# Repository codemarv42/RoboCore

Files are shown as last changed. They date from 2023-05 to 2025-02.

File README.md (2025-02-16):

# RoboCore

The RoboCore is basically a dual PCB solution, which is mounted on a chassis and takes over the evaluation and control of sensors and motors. Furthermore, this project was created by several people to develop the best robot for the RoboCup in the Rescue Line division. 

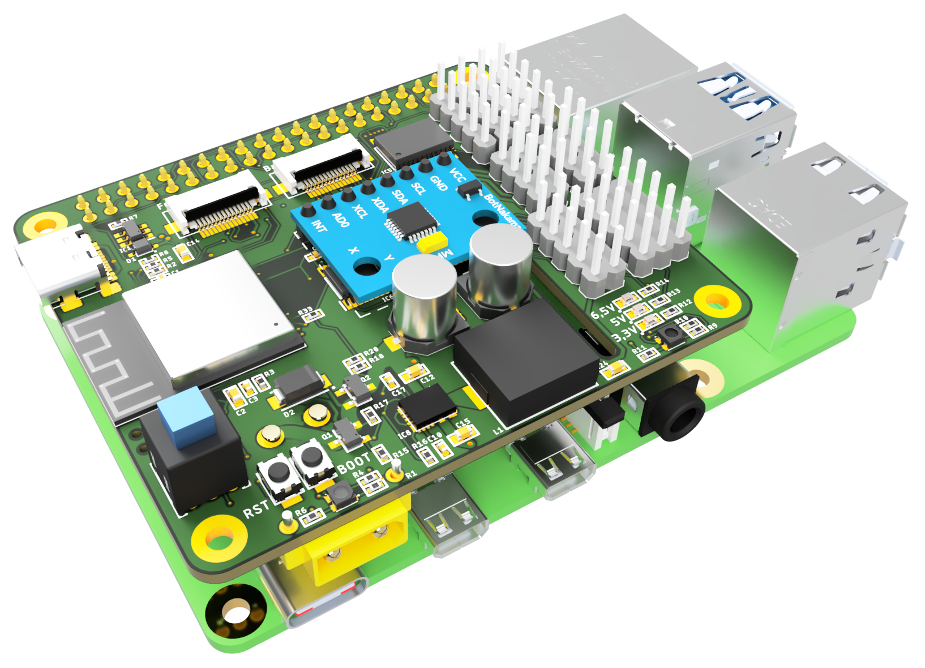
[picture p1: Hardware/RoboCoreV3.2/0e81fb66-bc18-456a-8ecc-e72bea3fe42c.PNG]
RoboCore V3.2


RoboCore embedded

# Hardware

A combination of two PCBs is used as our hardware, where the main PCB (RoboCoreV3.2) is plugged onto a Raspberry Pi and therefore forms the main control unit. The second circuit board (RoboLightV4.2) is installed on the underside of the robot and is responsible for measuring the light values on the line track. Below is our current hardware combination.

## To do list

- [x] Find Upload issue
- [x] Implement Boot and EN Buttons
- [x] Find ADC issue when using Neopixel LEDs
- [x] Voltage state LEDs
- [x] Inconsistent red-green difference of the LEDs

## Changelog

RoboCore:

- V3.2: Remove Neopixel led because of ADC problems, better voltage regulator for motor driver and further power management features
- V3.1: Raspberry PI hat design, external Display and buttons as user interface, ESP32-S3, two motor driver, Neopixel LED, Voltage regulator update
- V2: MPU6050 as secound PCB, dual light sensor bar, Pullup Fix near buttons
- V1: Inital Version

RoboLight:

- V4.3: Swap FCP pinout
- V4.2: Use regular RGB LEDs instead, better LED and phototransistor arrangement
- V4.1: Use Neopixel RGB LEDs instead, remove center photo transistor
- V3: Control Leds individual via a shiftregister
- V2: Fix distance between inner photo transistors
- V1: Inital Version

## Control unit PCB

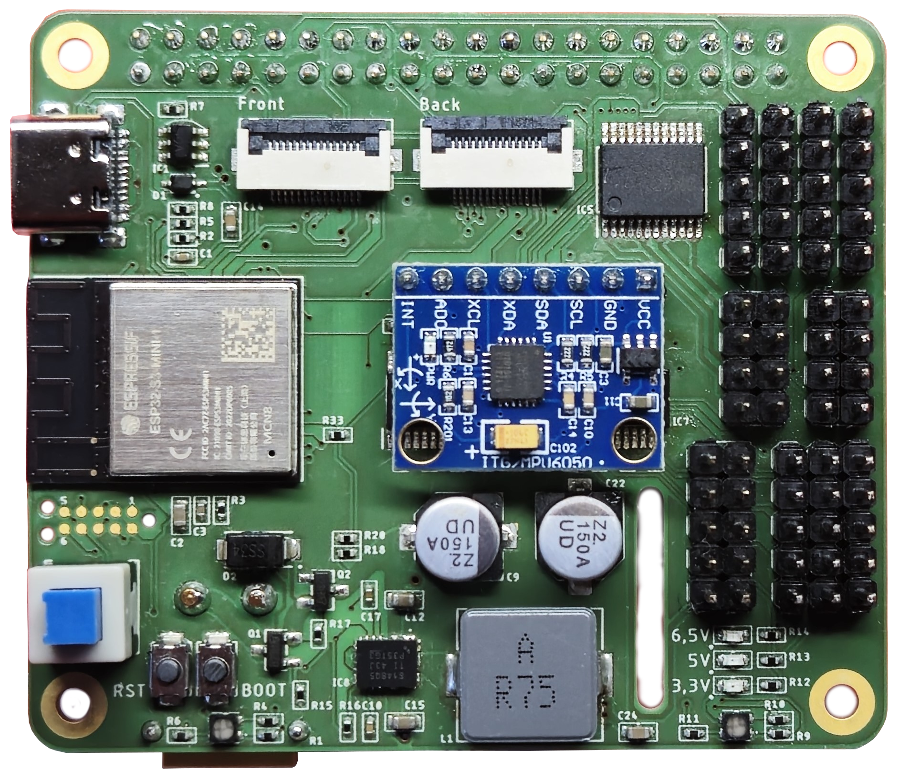
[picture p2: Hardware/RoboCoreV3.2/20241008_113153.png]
RoboCoreV3.2


Parameter for PCB (RoboCoreV3.2):

- Layer: 4
- Thickness: 1,6mm
- Length: 65,05mm
- Height: 56,03mm
- Minimum Copper Trace Width: 0,125mm

Pinout:

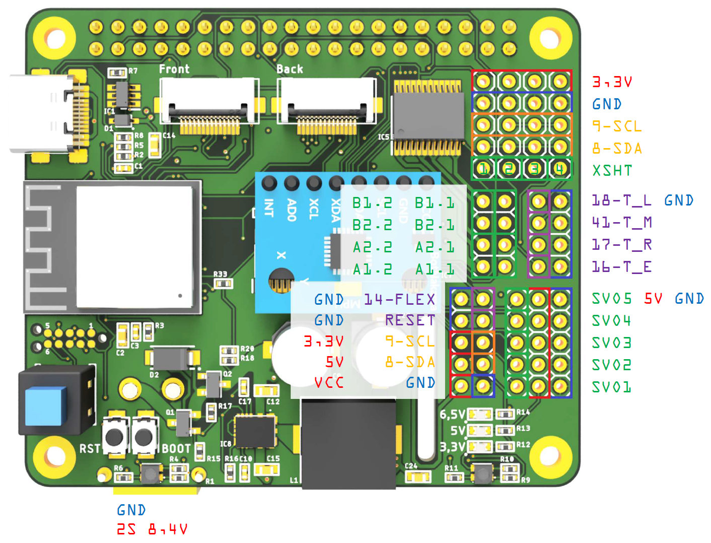
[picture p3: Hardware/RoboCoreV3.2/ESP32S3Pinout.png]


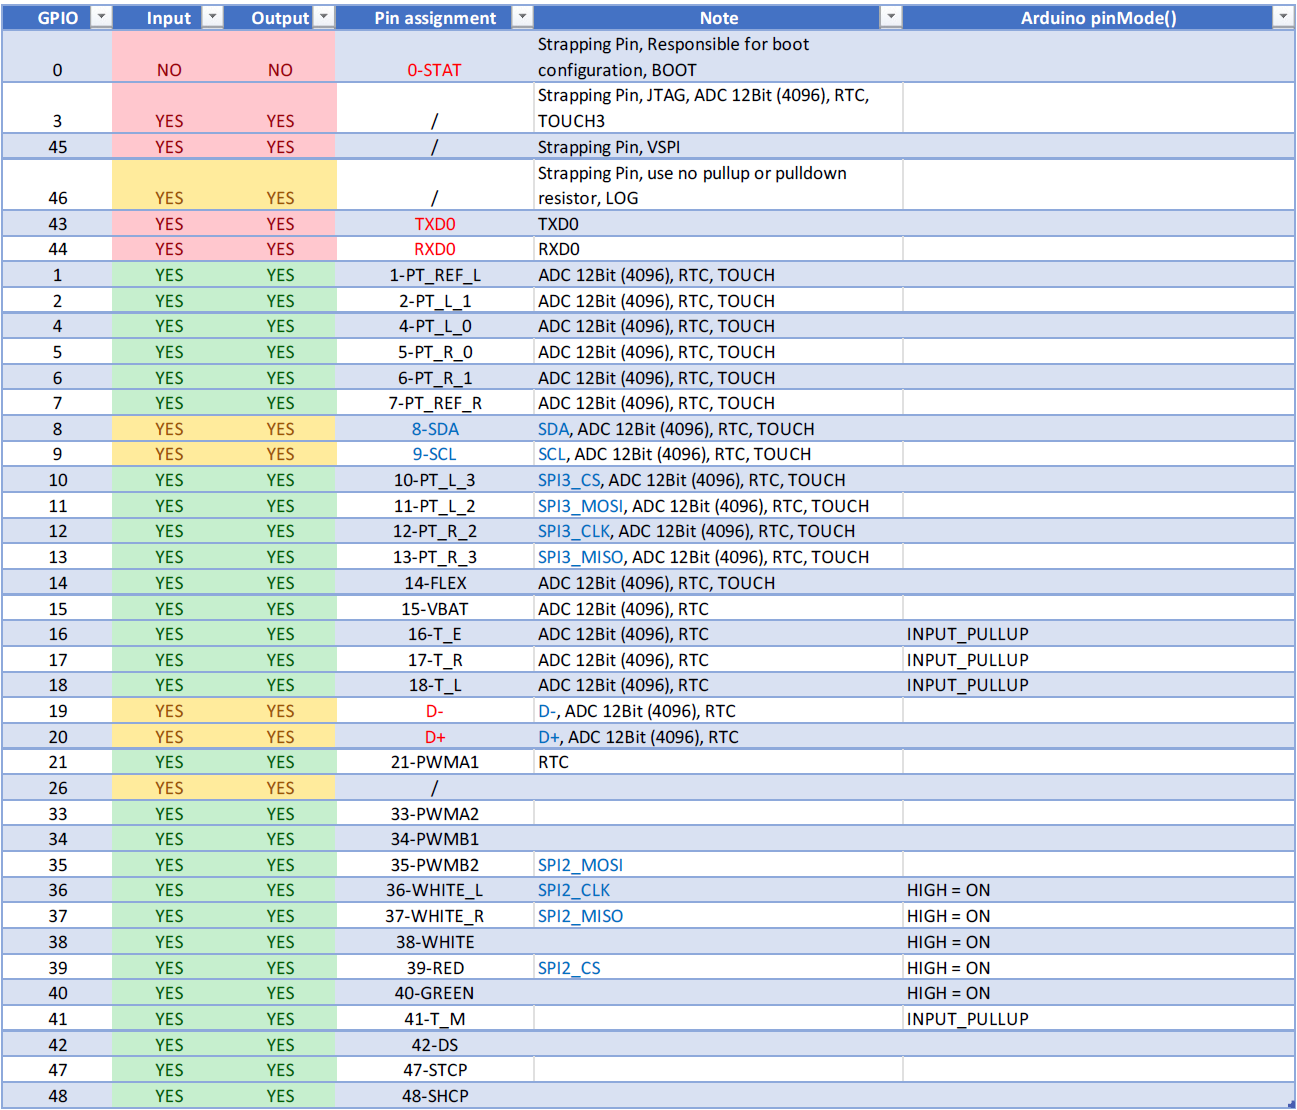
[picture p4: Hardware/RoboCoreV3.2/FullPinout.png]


## Light sensors PCB

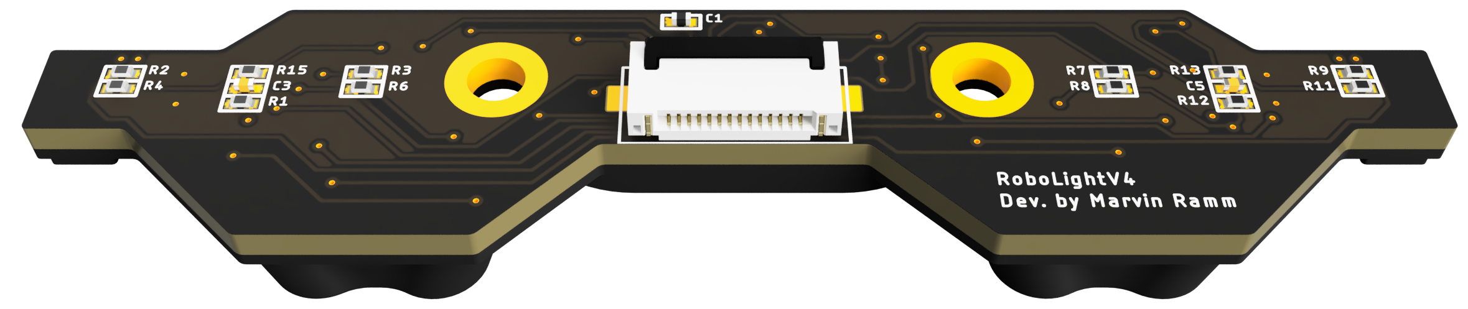
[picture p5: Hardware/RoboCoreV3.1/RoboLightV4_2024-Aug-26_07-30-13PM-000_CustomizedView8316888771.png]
RoboLightV4


Parameter for PCB (RoboLightV4.3):

- Layer: 2
- Thickness: 1,2mm / 1,6mm
- Length: 72,0mm
- Height: 15,23mm
- Minimum Copper Trace Width: 0,15mm

# Software

### You can find instructions for RoboCore V3.2 in PDF format here:
https://github.com/codemarv42/RoboCore/blob/main/Hardware/RoboCoreV3.2/RoboCoreV3.2%20Manual.pdf

## Required libraries

- Adafruit_GFX.h - https://github.com/adafruit/Adafruit-GFX-Library
- Adafruit_BusIO.h - https://github.com/adafruit/Adafruit_BusIO/tree/master
- Adafruit_PWMServoDriver.h - https://github.com/adafruit/Adafruit-PWM-Servo-Driver-Library
- Adafruit_SSD1306.h - https://github.com/adafruit/Adafruit_SSD1306
- MPU6050_light.h - https://github.com/rfetick/MPU6050_light
- VL53L1X.h - https://github.com/pololu/vl53l1x-arduino

## Download Mode

If no program can be uploaded to the ESP32-S3, it must be set to download mode. The following steps are necessary to do this:

1. Press and hold the BOOT and RESET button
2. Connect the RoboCore to the computer via USB
3. Release the RESET button while still holding the BOOT button
4. Release the BOOT button after a few seconds

## Compilation settings

To compile your program and then upload it to the RoboCore, some steps are necessary:

1. First you have to install the kernel of the ESP32 in Arduino: https://docs.espressif.com/projects/arduino-esp32/en/latest/installing.html
2. Next, the compilation settings must be specified. To do this, first select "ESP32S3 Dev Module" under Tools --> Board.
3. In the last step, the parameters of the ESP32 on the RoboCore must be set. To do this, select the following under Tools: 
- Board: "ESP32S3 Dev Module"
- USB CDC On Boot: "Enabled"
- CPU Frequency: "240MHz (WiFi/BT)"
- Flash Mode: "QIO 120MHz"
- Flash Size: "8MB (32Mb)"
- Partition Scheme: "8MB with SPIFFS"
- Erase all flash: "Disabled"
- Upload Speed: "921600"

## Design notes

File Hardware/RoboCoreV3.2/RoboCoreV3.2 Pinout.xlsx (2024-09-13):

ESP32-S3-MINI-1-N8
RoboCoreV3 | REV2
GPIO | Input | Output | Pin assignment | Note | Arduino pinMode() | https://www.espressif.com/sites/default/files/documentation/esp32-s3-mini-1_mini-1u_datasheet_en.pdf
0 | NO | NO | 0-STAT | Strapping Pin, Responsible for boot configuration, BOOT |  | https://diy.viktak.com/2023/11/esp32-s3-mini-1-development-board.html
3 | YES | YES | / | Strapping Pin, JTAG, ADC 12Bit (4096), RTC, TOUCH3
45 | YES | YES | / | Strapping Pin, VSPI
46 | YES | YES | / | Strapping Pin, use no pullup or pulldown resistor, LOG
43 | YES | YES | TXD0 | TXD0
44 | YES | YES | RXD0 | RXD0
1 | YES | YES | 1-PT_REF_L | ADC 12Bit (4096), RTC, TOUCH
2 | YES | YES | 2-PT_L_1 | ADC 12Bit (4096), RTC, TOUCH
4 | YES | YES | 4-PT_L_0 | ADC 12Bit (4096), RTC, TOUCH
5 | YES | YES | 5-PT_R_0 | ADC 12Bit (4096), RTC, TOUCH
6 | YES | YES | 6-PT_R_1 | ADC 12Bit (4096), RTC, TOUCH
7 | YES | YES | 7-PT_REF_R | ADC 12Bit (4096), RTC, TOUCH
8 | YES | YES | 8-SDA | SDA, ADC 12Bit (4096), RTC, TOUCH
9 | YES | YES | 9-SCL | SCL, ADC 12Bit (4096), RTC, TOUCH
10 | YES | YES | 10-PT_L_3 | SPI3_CS, ADC 12Bit (4096), RTC, TOUCH
11 | YES | YES | 11-PT_L_2 | SPI3_MOSI, ADC 12Bit (4096), RTC, TOUCH
12 | YES | YES | 12-PT_R_2 | SPI3_CLK, ADC 12Bit (4096), RTC, TOUCH
13 | YES | YES | 13-PT_R_3 | SPI3_MISO, ADC 12Bit (4096), RTC, TOUCH
14 | YES | YES | 14-FLEX | ADC 12Bit (4096), RTC, TOUCH
15 | YES | YES | 15-VBAT | ADC 12Bit (4096), RTC
16 | YES | YES | 16-T_E | ADC 12Bit (4096), RTC | INPUT_PULLUP
17 | YES | YES | 17-T_R | ADC 12Bit (4096), RTC | INPUT_PULLUP
18 | YES | YES | 18-T_L | ADC 12Bit (4096), RTC | INPUT_PULLUP
19 | YES | YES | D- | D-, ADC 12Bit (4096), RTC
20 | YES | YES | D+ | D+, ADC 12Bit (4096), RTC
21 | YES | YES | 21-PWMA1 | RTC
26 | YES | YES | /
33 | YES | YES | 33-PWMA2
34 | YES | YES | 34-PWMB1
35 | YES | YES | 35-PWMB2 | SPI2_MOSI
36 | YES | YES | 36-WHITE_L | SPI2_CLK | HIGH = ON
37 | YES | YES | 37-WHITE_R | SPI2_MISO | HIGH = ON
38 | YES | YES | 38-WHITE |  | HIGH = ON
39 | YES | YES | 39-RED | SPI2_CS | HIGH = ON
40 | YES | YES | 40-GREEN |  | HIGH = ON
41 | YES | YES | 41-T_M |  | INPUT_PULLUP
42 | YES | YES | 42-DS
47 | YES | YES | 47-STCP
48 | YES | YES | 48-SHCP

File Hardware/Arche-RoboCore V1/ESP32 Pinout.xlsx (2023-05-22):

GPIO | Input | Output | Belegt mit | Hinweis
0 | (OK) | (OK) | 0-BOOT | outputs PWM signal at boot
1 | X | (OK) | / | debug output at boot
2 | OK | OK | 2-T_L | LED
3 | (OK) | X | / | HIGH at boot
4 | OK | OK | 4-S0
5 | OK | OK | 5-S1 | outputs PWM signal at boot
6 | X | X | / | connected to the integrated SPI flash
7 | X | X | / | connected to the integrated SPI flash
8 | X | X | / | connected to the integrated SPI flash
9 | X | X | / | connected to the integrated SPI flash
10 | X | X | / | connected to the integrated SPI flash
11 | X | X | / | connected to the integrated SPI flash
12 | (OK) | OK | 12-S2 | boot fail if pulled high
13 | OK | OK | 13-S3
14 | OK | OK | 14-T_R | outputs PWM signal at boot
15 | OK | OK | 15-ENC_SW | outputs PWM signal at boot
16 | OK | OK | 16-SERVO4
17 | OK | OK | 17-SERVO3
18 | OK | OK | 18-SERVO2
19 | OK | OK | 19-SERVO1
21 | OK | OK | 21-SDA
22 | OK | OK | 22-SCL
23 | OK | OK | 23-PWMA
25 | OK | OK | 25-PWMB
26 | OK | OK | 26-METAL_S
27 | OK | OK | 27-SHCP
32 | OK | OK | 32-STCP
33 | OK | OK | 33-DS
34 | OK | X | 34-ENC_B
35 | OK | X | 35-ENC_A
36 | OK | X | 36-VBAT | ADC
39 | OK | X | 39-VOUT | ADC

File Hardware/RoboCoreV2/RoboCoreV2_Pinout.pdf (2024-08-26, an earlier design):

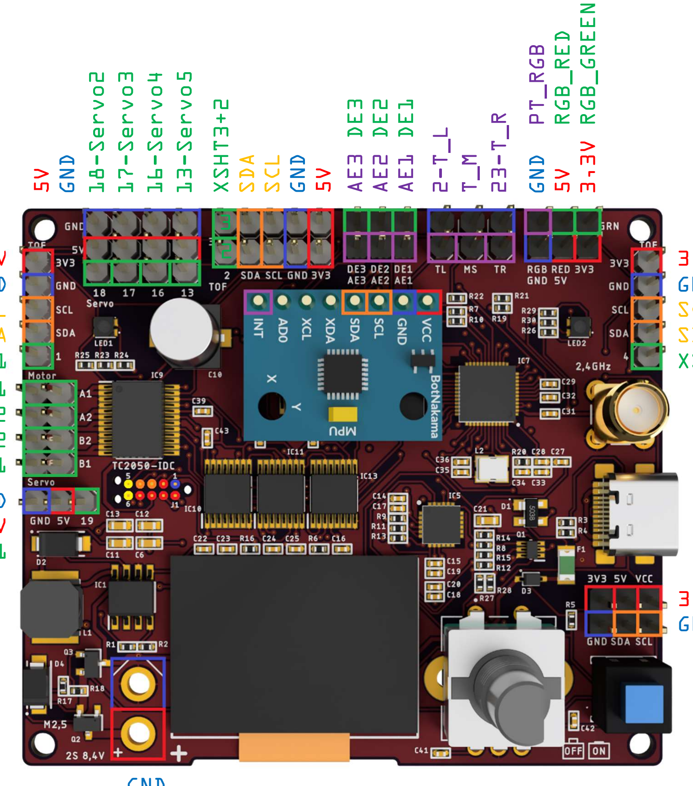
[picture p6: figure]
2 SDA SCL GND 5V

### 9. April 2024 1

# RoboCore V2 Pinout

Voltage
GND/Zero potential
Communication protocol
Digital output
Analog input

3,3V
GND
SCL
SDA
XSHT1
A1
A2
B2
B1

3,3V
GND
SCL
SDA
XSHT4

GND
5V

19-Servo1 5VGND 18-Servo2 17-Servo3 16-Servo4 13-Servo5 XSHT3

### 3 AE3 DE3 AE2 DE2 AE1 DE1 2-T_L T_M 23-T_R GND PT_RGB 5V RGB_RED 3,3V RGB_GREEN

3,3V 5V VCC
GND SDA SCL

GND
2S 8,4V

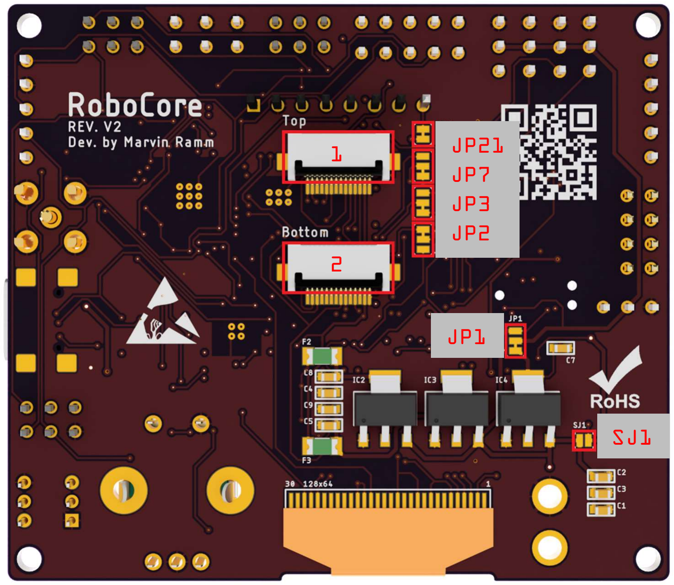
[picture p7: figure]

9. April 2024 | 2
Jumper name | Description
SJ1 | Can be connected if no voltage regulator is required for the motor driver.
JP1 | When switching the jumper, the servos are connected directly to the battery if no voltage regulator is used. Note that the servos can handle a maximum of 8.4V!
JP2 | This jumper must be switched if the "old" light sensor strip V2 wants to be used on the upper light sensor strip port.
JP3 | This jumper must be switched if the "old" light sensor strip V2 wants to be used on the upper light sensor strip port.
JP7 | This jumper must be switched if the "old" light sensor strip V2 wants to be used on the upper light sensor strip port.
JP21 | This jumper can be cut if you do not want to use the interrupt function of the MPU6050.

* All JPs are jumpers, where one side is normally connected. This connection must be cut when the other side of the jumper will be connected!

9. April 2024 | 3
ESP32 GPIO | Pin Name | Description
2 | 2-T_L | An input pull-up must be defined in the software! Buttons can be connected to this pin, in which case a LOW is present when the button is pressed.
4 | 4-S0 | Used to select the multiplexer output.
5 | 5-S1 | Used to select the multiplexer output.
12 | 12-S2 | Used to select the multiplexer output.
13 | 13-SERVO5 | A servo can be connected to this pin.
14 | 14-S3 | Used to select the multiplexer output.
15 | 15-ENC_SW | An input pull-up must be defined in the software! This pin is connected to the encoder button, which goes LOW when pressed.
16 | 16-SERVO4 | A servo can be connected to this pin.
17 | 17-SERVO3 | A servo can be connected to this pin.
18 | 18-SERVO2 | A servo can be connected to this pin.
19 | 19-SERVO1 | A servo can be connected to this pin.
21 | 21-SDA | Data lines for I2C.
22 | 22-SCL | Data lines for I2C.
23 | 23-T_R | An input pull-up must be defined in the software! Buttons can be connected to this pin, in which case a LOW is present when the button is pressed.
25 | 25-PWMB | This pin determines the motor speed.
26 | 26-PWMA | This pin determines the motor speed.
27 | 27-SHCP | Controls data shifting within the register.
32 | 32-STCP | Latches shifted data into output registers.
33 | 33-DS | New data enters the register.
34 | 34-ENC_B | Outputs a square wave signal 90 degrees out of phase with Pin A.

9. April 2024 | 4
35 | 35-ENC_A | Outputs a square wave signal in phase with encoder rotation.
36 | 36-VBAT | The battery voltage can be measured with this pin.
39 | 39-VOUT | The voltage of the multiplexer is applied to this pin.
Multiplexer GPIO | Pin Name | Description
I0 | PT_REF_L | Reflection sensor left.
I1 | PT_L_1 | Light sensor left outside.
I2 | PT_L_0 | Light sensor left inside.
I3 | PT_M | Light sensor center.
I4 | PT_R_0 | Light sensor right inside.
I5 | PT_R_1 | Light sensor right outside.
I6 | PT_REF_R | Reflection sensor right.
I7 | PT_RGB | 90° RGB sensor.
I8 | PT_L_3 | Light sensor left outside.
I9 | PT_L_2 | Light sensor left inside.
I10 | PT_R_2 | Light sensor right inside.
I11 | PT_R_3 | Light sensor right outside.
I12 | T_M | Button center or metal sensor.
I13 | AE1 | External analog pin.
I14 | AE2 | External analog pin.
I15 | AE3/INT | External analog pin / MPU6050 interrupt (LOW when new data is available)

*PT_L_3-PT_R_3 belong to the second light sensor strip (V2)

Shiftregister GPIO | Pin Name | Description
Q0,0 | AIN1 | Determines the motor direction.
Q1,0 | AIN2 | Determines the motor direction.
Q2,0 | BIN1 | Determines the motor direction.
Q3,0 | BIN2 | Determines the motor direction.

### 9. April 2024

5

Q4,0 | STBY | If the pin is set LOW, the motor driver is off and at HIGH it is on.
Q5,0 | LED_L_RED | Status LED left red. LOW = ON
Q6,0 | LED_L_GREEN | Status LED left green.
Q7,0 | LED_L_BLUE | Status LED left blue .
Q0,1 | LED_R_RED | Status LED right red .
Q1,1 | LED_R_GREEN LED_R_BLUE | Status LED right green. Q2,1 Status LED right blue.
Q3,1 | XSHT1 | A HIGH activates the TOF sensor .
Q4,1 | XSHT2 | A HIGH activates the TOF sensor .
Q5,1 | XSHT3 | A HIGH activates the TOF sensor.
Q6,1 | XSHT4 | A HIGH activates the TOF sensor.
Q7,1 | RGB_RED | 90° RGB sensor LED red. LOW = ON
Q0,2 | RGB_GREEN | 90° RGB sensor LED green .
Q1,2 | PT_WHITE | Light sensor strip LED white. HIGH = ON
Q2,2 | PT_RED | Light sensor strip LED red.
Q3,2 | PT_GREEN | Light sensor strip LED green.
Q4,2 | PT_BLUE | Light sensor strip LED blue.
Q5,2 | DE1 | External digital pin .
Q6,2 | DE 2 External digital pin | .
Q7,2 | DE3 | External digital pin.
Q0,3 | LED_RED | Red LED of light sensor strip 1 (V3). LOW = ON
Q1,3 | LED_GREEN | Green LED of light sensor strip 1 (V3).
Q2,3 | LED_L_1 | LED of sensor L_1 of the light sensor strip 1 (V3) .
Q3,3 | LED_L_0 | LED of sensor L_0 of the light sensor strip 1 (V3) .
Q4,3 | LED_M | LED of sensor M of the light sensor strip 1 (V3) .
Q5,3 | LED_R_0 | LED of sensor R_0 of the light sensor strip 1 (V3) .
Q6,3 | LED_R_1 | LED of sensor R_1 of the light sensor strip 1 (V3) .
Q7,3 | LED_REF | LEDs of sensor REF of the light sensor strip 1 (V3) .

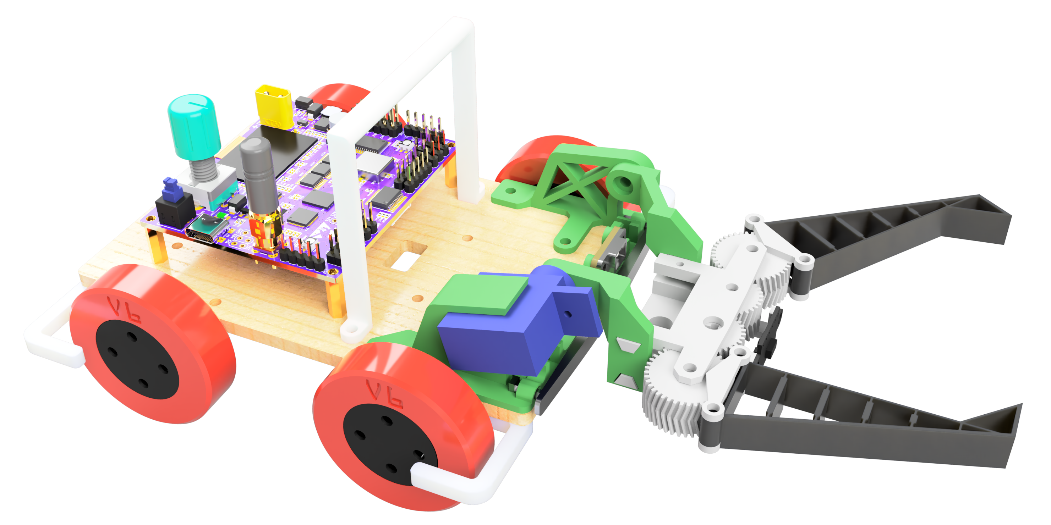
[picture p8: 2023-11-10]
Hardware/Chassis and 3D models/b26accad-7b25-4acc-98aa-736cbc8c62c4.PNG

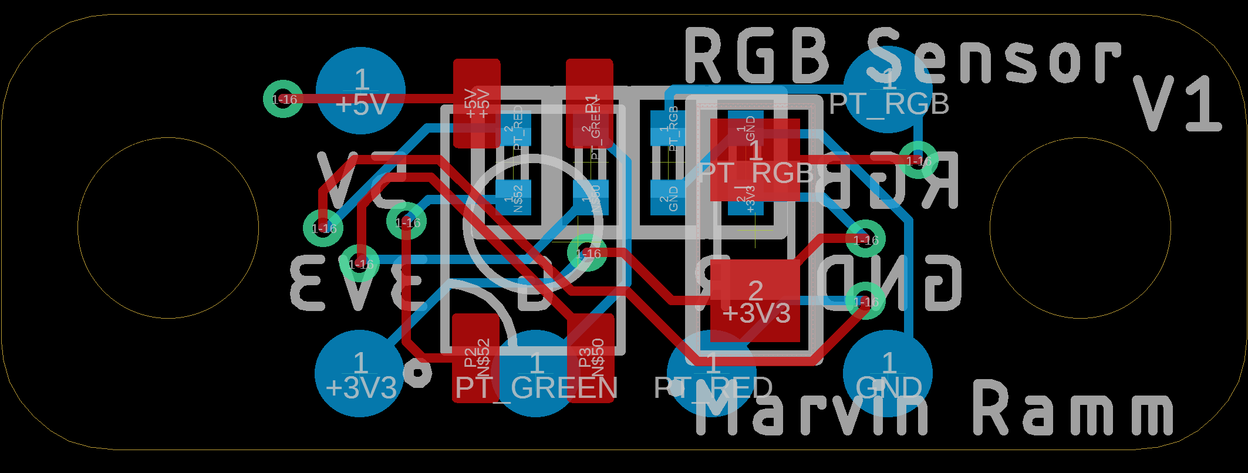
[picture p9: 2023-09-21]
Hardware/RGB Sensor V1/RGB Sensor V1_2.png

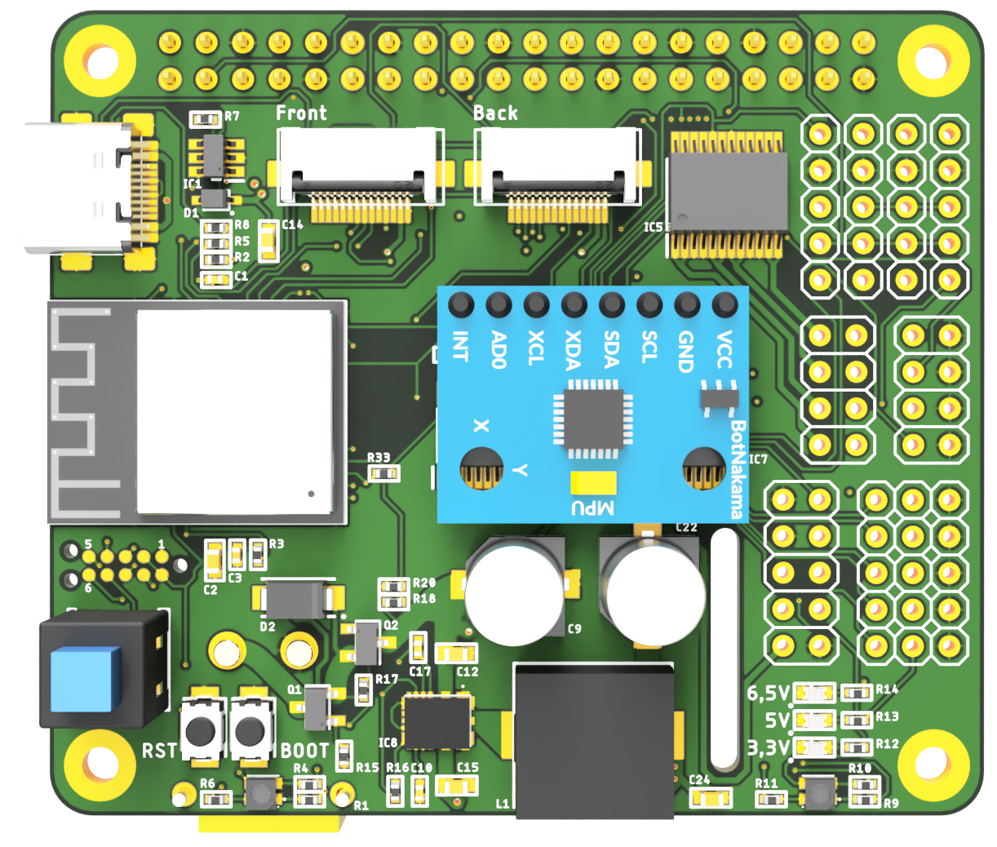
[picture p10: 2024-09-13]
Hardware/RoboCoreV3.2/bfed8ac9-45c9-460a-93a3-c1a7623437e7.PNG

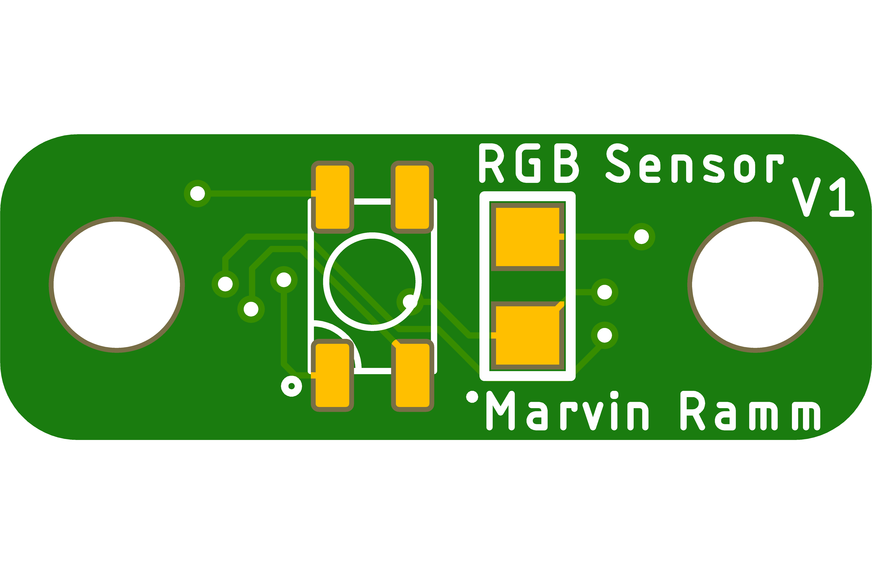
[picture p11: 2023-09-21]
Hardware/RGB Sensor V1/RGB Sensor V1_3.png

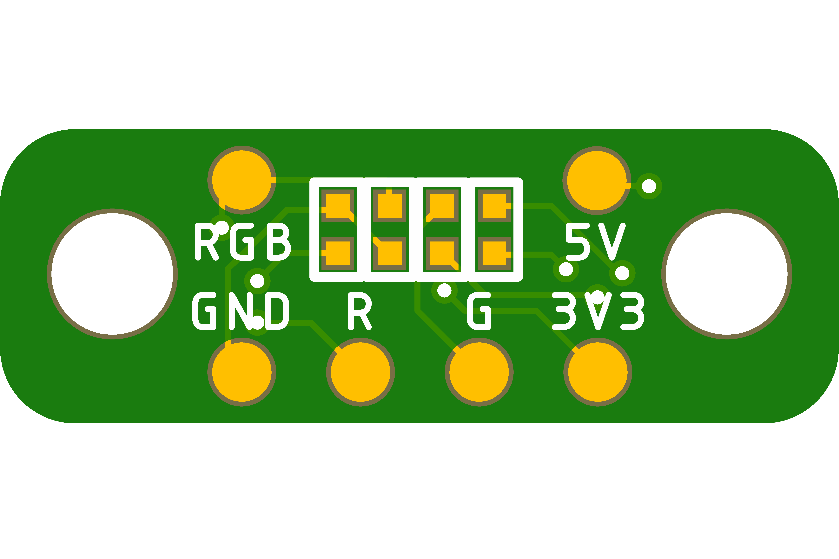
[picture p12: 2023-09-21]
Hardware/RGB Sensor V1/RGB Sensor V1_4.png

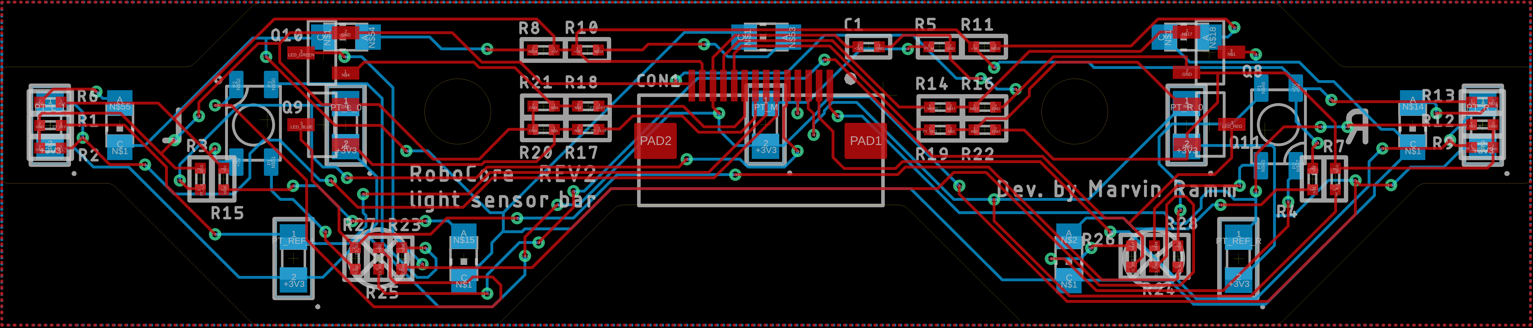
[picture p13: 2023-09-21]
Hardware/RoboCore light sensor bar V2/RoboCore Light sensor bar_1.png

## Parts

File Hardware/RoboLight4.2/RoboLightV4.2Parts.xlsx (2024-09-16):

RoboLightV4.2 Parts
Qty | Value | Parts
1 | 1uF | C1
1 | FC05-S14FCT-00 | CON1
2 | 2,2k | R1, R6
2 | FM-B2020RGBA-HG | LED5, LED8
4 | 5,1k | R2, R3, R4, R5
6 | XL-2012WWC | LED1, LED2, LED3, LED4, LED6, LED7
6 | PT17-21C/L41/TR8 | Q1, Q2, Q3, Q4, Q5, Q6
10 | 150 | R11, R12, R15, R16, R7, R8, R9, R10, R13, R14

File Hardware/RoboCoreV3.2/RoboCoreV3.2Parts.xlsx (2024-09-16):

RoboCoreV3.2 Parts
Qty | Value | Parts
1 | PINH2X5 | JP13
1 | 100pF | C21
1 | 10K | R3
1 | 2,2K | R20
1 | 4,7uF | C14
1 | 5,1K | R18
1 | 51 | R22
1 | AMS1117-3.3 | IC10
1 | ASPIAIG-F1040-R75M-T | L1
1 | BAT60A | D1
1 | Blue | LED5
1 | ESP32-S3-MINI-1-N8 | IC2
1 | Green | LED4
1 | LM61480Q5RPHRQ1 | IC8
1 | MPU6050_MODULE | IC11
1 | PCA9685PW | IC7
1 | PINHD-2X20 | JP2
1 | Red | LED3
1 | SRV05-4MR6T1G | IC1
1 | SS34A | D2
1 | TC2050-IDC-NL_ESP32 | J2
1 | TLC-NSMD100 | F1
1 | TPS54302DDCR | IC9
1 | TYPE-C-31-M-14 | U1
1 | XKB7070-Z-92 | SW3
1 | XT30PW-M | J1
1 | YNR6045-3R3N | L2
2 | PINH2X4 | JP1, JP12
2 | 330 | R6, R11
2 | 74HC595PW,118 | IC3, IC6
2 | FC05-S14FCT-00 | CON1, CON2
2 | FM-B2020RGBA-HG | LED1, LED2
2 | TB6612FNG,C,8,EL | IC4, IC5
2 | TS-1088-AR02016 | SW1, SW2
2 | UUD1A151MCL1GS | C9, C22
3 | 10K | R7, R19, R33
3 | 1uF | C1, C3, C10
3 | 5,1K | R2, R5, R8
3 | IRLML9303TRPBF-VB | Q1, Q2, Q3
4 | PINHD5 | JP3, JP4, JP5, JP6
4 | 1K | R12, R13, R14, R23
4 | 330 | R1, R4, R9, R10
5 | PINHD-1X3 | JP7, JP8, JP9, JP10, JP11
5 | 10 | R28, R29, R30, R34, R35
5 | SI2302DDS-T1-GE3 | Q4, Q5, Q6, Q7, Q8
7 | TEST-POINT3X5 | TP1, TP3, TP5, TP6, TP7, TP8, TP9
8 | 0,1uF | C4, C5, C6, C7, C8, C11, C16, C17
10 | 100K | R15, R16, R17, R21, R24, R25, R26, R27, R31, R32
10 | 10uF | C2, C12, C13, C15, C18, C19, C20, C23, C24, C25

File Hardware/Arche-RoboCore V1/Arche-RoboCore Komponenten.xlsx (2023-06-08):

Stüc | kliste exportiert aus | C:/Users/marvi/Documents/EAGLE/projects/ | Arche-RoboCore/Arche-RoboCore | .sch am 22.05.2023 13:40
Qty | Value | Device | Package | Parts |  |  | Description | ARROW_PART_NUMBER ARROW_PRICE-STOCK BUILT_BY COPYRIGHT DATASHEET DESCRIPTION | HEIGHT J MANUFACTURER_NAME MANUFACTURER_PART_NUMBER MOUSER_PART_NUMBER MOUSER_PRICE-STOCK MOUSER_TESTING_PART_NUMBER MOUSER_TESTING_PRICE-STOCK POPULARITY SOURCELIBRARY SPICEPREFIX VALUE VENDOR
3 |  | PINHD-1X2 | 1X02 | JP3, JP6, JP8 |  |  | PIN HEADER |  | 98
4 |  | PINHD-1X3 | 1X03 | JP11, JP12, JP14, JP15 |  |  | PIN HEADER |  | 92
4 |  | PINHD-1X5 | 1X05 | JP2, JP5, JP7, JP9 |  |  | PIN HEADER |  | 69
3 |  | PINHD-2X3 | 2X03 | JP4, JP16, JP17 |  |  | PIN HEADER |  | 62
1 |  | PINHD-2X4 | 2X04 | JP1 |  |  | PIN HEADER |  | 47
7 | 0,1uF | C_0402 | C0402 | C10, C11, C17, C18, C19, | C20, | C22 | NON-POLARIZED | CAP
5 | 0,1µF | C_0402 | C0402 | C29, C33, C34, C37, C41 |  |  | NON-POLARIZED | CAP
7 | 100k? | R_0402 | R0402 | R12, R13, R15, R16, R22, | R25, | R26 | RESISTOR
2 | 100nF | C_0402 | C0402 | C15, C46 |  |  | NON-POLARIZED | CAP
2 | 100pF | C_0402 | C0402 | C16, C32 |  |  | NON-POLARIZED | CAP
16 | 10k? | R_0402 | R0402 | R3, R4, R8, R9, R11, R14 | , R17 | , R19, R20, R23, R24, R28, R35, R36, R37, R38 | RESISTOR
4 | 10nF | C_0402 | C0402 | C26, C47, C48, C50 |  |  | NON-POLARIZED | CAP
10 | 10µF | C_0603 | C0603 | C4, C6, C7, C8, C9, C14, | C31, | C35, C36, C49 | NON-POLARIZED | CAP
2 | 12pF | C_0402 | C0402 | C28, C30 |  |  | NON-POLARIZED | CAP
2 | 1uF | C_0402 | C0402 | C21, C51 |  |  | NON-POLARIZED | CAP
7 | 1µF | C_0402 | C0402 | C38, C39, C40, C42, C43, | C44, | C45 | NON-POLARIZED | CAP
7 | 2,2k? | R_0402 | R0402 | R5, R29, R30, R31, R32, | R33, | R34 | RESISTOR
1 | 20k? | R_0402 | R0402 | R10 |  |  | RESISTOR
1 | 22k? | R_0402 | R0402 | R7 |  |  | RESISTOR
2 | 270pF | C_0402 | C0402 | C24, C25 |  |  | NON-POLARIZED | CAP
1 | 2864KSWE_128X64I2C | 2864KSWE_128X64I2C | 2864KSWE_128X64I2C | DSP1 |  |  |  |  | 2864KSWE_128X64I2C
1 | 33k? | R_0402 | R0402 | R6 |  |  | RESISTOR
1 | 390k? | R_0402 | R0402 | R21 |  |  | RESISTOR
1 | 3nF | C_0402 | C0402 | C27 |  |  | NON-POLARIZED | CAP
2 | 4,7uF | C_0402 | C0402 | C12, C13 |  |  | NON-POLARIZED | CAP
3 | 4,7µF | C_0603 | C0603 | C1, C2, C3 |  |  | NON-POLARIZED | CAP
2 | 5,1k? | R_0402 | R0402 | R1, R2 |  |  | RESISTOR
1 | 5,6pF | C_0402 | C0402 | C23 |  |  | NON-POLARIZED | CAP
1 | 5-1814832-2 | 5-1814832-2 | 518148322 | J1 |  |  | RF Connectors | , SMA RF Interface, Jack, RF Connector Mated Outer Diameter (Approximate) .25 in [6.35 mm], 50 , Threaded, 3GHz Operating Frequency 5-1814832-2 https://www.arrow.com/en/products/5-1814832-2/te-connectivity?region=europe RF Connectors, SMA RF Interface, Jack, RF Connector Mated Outer Diameter (App | roximate) .25 in [6.35 mm], 50 , Threaded, 3GHz Operating Frequency 9.5mm TE Connectivity 5-1814832-2 571-5-1814832-2 https://www.mouser.co.uk/ProductDetail/TE-Connectivity/5-1814832-2?qs=Cb2nCFKsA8rPOrkEMAAQ4A%3D%3D
1 | 64,9k? | R_0402 | R0402 | R27 |  |  | RESISTOR
3 | 74HC595PW,118 | 74HC595PW,118 | SOP65P640X110-16N | IC10, IC12, IC13 |  |  | 74HC(T)595 - | 8-bit serial-in, serial or parallel-out shift register with output latches; 3-state@en-us 74HC595PW,118 https://www.arrow.com/en/products/74hc595pw118/nexperia?region=asia 74HC(T)595 - 8-bit serial-in, serial or parallel-out shift register with outp | ut latches 3-state@en-us 1.1mm Nexperia 74HC595PW,118 771-74HC595PW-T https://www.mouser.co.uk/ProductDetail/Nexperia/74HC595PW118?qs=P62ublwmbi8GOYhe4PjE9Q%3D%3D
1 | 75k? | R_0402 | R0402 | R18 |  |  | RESISTOR
3 | AMS1117-3.3 | AMS1117-3.3 | SOT229P700X180-4N | IC1, IC2, IC3 |  |  | 1A LOW DROPOU | T VOLTAGE REGULATOR, SOT-223 AMS1117-3.3 1A LOW DROPOUT VOLTAGE REGULATOR, SOT-223 | 1.8mm Advanced Monolithic Systems AMS1117-3.3
2 | AO3407A | AO3407A | SOT95P280X125-3N | Q1, Q2 |  |  | MOSFET P-CH 3 | 0V 4.3A SOT23 AO3407A https://www.arrow.com/en/products/ao3407a/alpha-and-omega-semiconductor MOSFET P-CH 30V 4.3A SOT23 | 1.25mm Alpha & Omega Semiconductors AO3407A
3 | BLM18PG121SN1D | BLM18PG121SN1D | BLM18AG102BH1D | FL1, FL2, FL3 |  |  | Ferrite bead | SMD 0603 120R 2A Murata Ferrite Bead (Chip Ferrite Bead), 1.6 x 0.8 x 0.8mm (0603), 120 impedance at 100 MHz BLM18PG121SN1D https://www.arrow.com/en/products/blm18pg121sn1d/murata-manufacturing?region=nac Ferrite bead SMD 0603 120R 2A Murata Ferrite Bead (Chip Ferrite Bead), 1.6 x | 0.8 x 0.8mm (0603), 120 impedance at 100 MHz 0.95mm Murata Electronics BLM18PG121SN1D 81-BLM18PG121SN1D https://www.mouser.co.uk/ProductDetail/Murata-Electronics/BLM18PG121SN1D?qs=tY8e8KZalarVxhnmnUYZ1A%3D%3D
1 | CD74HC4067SM96 | CD74HC4067SM96 | SOP65P780X200-24N | IC8 |  |  | High Speed CM | OS 16-Ch MUX/DEMUX 24P SOIC CD74HC4067SM96, Multiplexer/Demultiplexer Single 16:1, 3 V, 5 V, 24-Pin, SSOP, 1 CD74HC4067SM96 https://www.arrow.com/en/products/cd74hc4067sm96/texas-instruments?region=nac High Speed CMOS 16-Ch MUX/DEMUX 24P SOIC CD74HC4067SM96, Multiplexer/Demultip | lexer Single 16:1, 3 V, 5 V, 24-Pin, SSOP, 1 2mm Texas Instruments CD74HC4067SM96 595-CD74HC4067SM96 https://www.mouser.co.uk/ProductDetail/Texas-Instruments/CD74HC4067SM96?qs=JHHQeKcAU3DyfvAOSRLjhQ%3D%3D
1 | CP2102N-A02-GQFN24R | CP2102N-A02-GQFN24R | QFN50P400X400X80-25N | IC4 |  |  | USB Interface | IC USB to UART bridge - QFN24 CP2102N-A02-GQFN24R https://www.arrow.com/en/products/cp2102n-a02-gqfn24r/silicon-labs USB Interface IC USB to UART bridge - QFN24 | 0.8mm Silicon Labs CP2102N-A02-GQFN24R 634-CP2102NA02QFN24R https://www.mouser.co.uk/ProductDetail/Silicon-Labs/CP2102N-A02-GQFN24R?qs=u16ybLDytRaIVBf0X4zL0g%3D%3D X
1 | ESP32-D0WDQ6 | ESP32-D0WDQ6 | QFN40P600X600X90-49N | IC9 |  |  | RF System on | a Chip - SoC SMD IC ESP32-D0WDQ6, Dual Core MCU, WiFi & Bluetooth Combo, QFN48-pin, 6*6mm RF System on a Chip - SoC SMD IC ESP32-D0WDQ6, Dual Core MCU, WiFi & Bluetoot | h Combo, QFN48-pin, 6*6mm 0.9mm Espressif Systems ESP32-D0WDQ6 356-ESP32-D0WDQ6 https://www.mouser.co.uk/ProductDetail/Espressif-Systems/ESP32-D0WDQ6?qs=chTDxNqvsykWgzfXx0gR%252BQ%3D%3D
1 | FC05-S14FCT-00 | FC05-S14FCT-00 | FC05-S14FCT-00 | CON1
2 | JUMPER-SMT_2_NO_SILK | JUMPER-SMT_2_NO_SILK | SMT-JUMPER_2_NO_SILK | JP10, JP13 |  |  | Normally open | jumper
1 | LQH5BPB100MT0L | LQH5BPB100MT0L | LQH5BPB100MT0L | L2 |  |  | LQH5BPB_T0 Se | ries Inductor 10uH +/-20% 2020 (5050) LQH5BPB_T0 Series Inductor 10uH +/-20% 2020 (5050) | 2.2mm Murata Electronics LQH5BPB100MT0L 81-LQH5BPB100MT0L https://www.mouser.co.uk/ProductDetail/Murata-Electronics/LQH5BPB100MT0L?qs=hNud%2FORuBR2eSUAobsF5Ww%3D%3D
1 | MMDT3904-TP | MMDT3904-TP | SOT65P230X120-6N | IC6 |  |  | Bipolar Trans | istors - BJT 200mA 40V MMDT3904-TP https://www.arrow.com/en/products/mmdt3904-tp/micro-commercial-components?region=nac Bipolar Transistors - BJT 200mA 40V | 1.2mm Micro Commercial Components (MCC) MMDT3904-TP 833-MMDT3904-TP https://www.mouser.co.uk/ProductDetail/Micro-Commercial-Components-MCC/MMDT3904-TP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
1 | MP1584EN-LF-Z | MP1584EN-LF-Z | SOIC127P600X170-9N | IC11 |  |  | Switching Vol | tage Regulators 3A 1.5MHz 28V Nonsync Buck Switching Voltage Regulators 3A 1.5MHz 28V Nonsync Buck | 1.7mm Monolithic Power Systems (MPS) MP1584EN-LF-Z 946-MP1584ENLFZ https://www.mouser.co.uk/ProductDetail/Monolithic-Power-Systems-MPS/MP1584EN-LF-Z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
1 | MPU-6050 | MPU-6050 | QFN50P400X400X95-25N | IC14 |  |  | Gyro & Accele | rometer 6 Axis I2C,MEMs InvenSense MPU-6050 6-Axis Motion Sensor Module MPU-6050 https://www.arrow.com/en/products/mpu-6050/invensense Gyro & Accelerometer 6 Axis I2C,MEMs InvenSense MPU-6050 6-Axis Motion Sensor | Module 0.95mm InvenSense Inc. MPU-6050 N/A http://www.mouser.com/Search/ProductDetail.aspx?qs=u4fy%2fsgLU9O14B5JgyQFvg%3d%3d
3 | NANOSMDC020F-2 | NANOSMDC020F-2 | FUSC3216X82N | F1, F2, F3 |  |  | LITTELFUSE - | NANOSMDC020F-2 - POLYSWITCH, SMD, 1206, 0.2A NANOSMDC020F-2 https://www.arrow.com/en/products/nanosmdc020f-2/littelfuse LITTELFUSE - NANOSMDC020F-2 - POLYSWITCH, SMD, 1206, 0.2A | 0.82mm LITTELFUSE NANOSMDC020F-2 650-NANOSMDC020F-2 https://www.mouser.co.uk/ProductDetail/Littelfuse/NANOSMDC020F-2?qs=iK0evp%252BCRRU6agwMt7HYjg%3D%3D
1 | PEC12R-4230F-S0024 | PEC12R-4230F-S0024 | PEC12R4230FS0024 | ENC1 |  |  | Encoder 30mm | Shaft w/Switch 24 pulses Bourns 24 Pulse Incremental Mechanical Rotary Encoder with a 6 mm Flat Shaft, Through Hole PEC12R-4230F-S0024 https://www.arrow.com/en/products/pec12r-4230f-s0024/bourns?region=nac Encoder 30mm Shaft w/Switch 24 pulses Bourns 24 Pulse Incremental Mechanical | Rotary Encoder with a 6 mm Flat Shaft, Through Hole 30.5mm Bourns PEC12R-4230F-S0024 652-PEC12R-4230F-S24 https://www.mouser.co.uk/ProductDetail/Bourns/PEC12R-4230F-S0024?qs=Zq5ylnUbLm78S3yGzO6hng%3D%3D
2 | RGBLED | RGBLED | RGBLED | RGB1, RGB2
1 | SMD-3225_4P16MHZ_20PF | _10PPM_-4 SMD-3225_4P16MHZ_20PF_10PPM_-4 | SMD3225_4P16MHZ20PF10PPM4085 | L1 |  |  | SMD-3225_4P16 | MHZ 20PF 10PPM -40~+85 SMD-3225_4P16MHZ 20PF 10PPM -40~+85 | 0.8mm TAE(Zhejiang Abel Elec) SMD-3225_4P16MHZ 20PF 10PPM -40~+85?
1 | SP0503BAHTG | SP0503BAHTG | SP0503BAHTG | D1 |  |  | ESD Suppresso | rs / TVS Diodes TVS AVAL DIODE SMT SP0503BAHTG https://www.arrow.com/en/products/sp0503bahtg/littelfuse?region=nac ESD Suppressors / TVS Diodes TVS AVAL DIODE SMT | 1.22mm LITTELFUSE SP0503BAHTG 576-SP0503BAHTG https://www.mouser.co.uk/ProductDetail/Littelfuse/SP0503BAHTG?qs=uD%2FdkN7XIa0NTYXwHdELYA%3D%3D
3 | SS34A | SS34A | DIOM5026X262N | D2, D3, D4 |  |  | MULTICOMP - S | S34A - DIODE, RECTIFIER, 3A, 40V, DO-214AC MULTICOMP - SS34A - DIODE, RECTIFIER, 3A, 40V, DO-214AC | 2.62mm MULTICOMP SS34A
1 | TB6612FNG,C,8,EL | TB6612FNG,C,8,EL | SOP65P760X160-24N | IC5 |  |  | otor / Motion | / Ignition Controllers & Drivers Brush Motor Driver IC TB6612FNG,C,8,EL https://www.arrow.com/en/products/tb6612fngc8el/toshiba?region=nac otor / Motion / Ignition Controllers & Drivers Brush Motor Driver IC | 1.6mm Toshiba TB6612FNG,C,8,EL 757-TB6612FNGC8EL https://www.mouser.co.uk/ProductDetail/Toshiba/TB6612FNGC8EL?qs=rsevcuukUAy2UalRuv4E%2FQ%3D%3D
12 | TEST-POINT3X5 | TEST-POINT3X5 | PAD.03X.05 | TP1, TP3, TP4, TP5, TP6, | TP7, | TP8, TP9, TP10, TP11, TP12, TP13 | SparkFun Test | Points
1 | TYPE-C-31-M-14 | TYPE-C-31-M-14 | TYPE-C-31-M-14_HRO | U1 |  |  |  | EMA_Cory Copyright (C) 2018 Accelerated Designs. All rights reserved https://datasheet.lcsc.com/szlcsc/1811101526_Korean-Hroparts-Elec-TYPE-C-31-M-14_C223907.pdf | TYPE-C-31-M-14 HRO_Parts_Electronics_2020-03-18 HRO Electronics
1 | UUD1C151MCL1GS | UUD1C151MCL1GS | CAPAE660X800N | C5 |  |  | Cap Aluminum | Lytic 150uF 16V 20% (6.3 X 7.7mm) SMD 280mA 2000h 105C Automotive T/R UUD1C151MCL1GS https://www.arrow.com/en/products/uud1c151mcl1gs/nichicon Cap Aluminum Lytic 150uF 16V 20% (6.3 X 7.7mm) SMD 280mA 2000h 105C Automotiv | e T/R 8mm Nichicon UUD1C151MCL1GS 647-UUD1C151MCL https://www.mouser.com/Search/Refine.aspx?Keyword=647-UUD1C151MCL
1 | W25Q128JVPIQ | W25Q128JVPIQ | SON127P800X600X80-9N | IC7 |  |  | IC FLASH 128M | SPI 133MHZ 8WSON W25Q128JVPIQ https://www.arrow.com/en/products/w25q128jvpiq/winbond-electronics?region=nac IC FLASH 128M SPI 133MHZ 8WSON | 0.8mm Winbond W25Q128JVPIQ 454-W25Q128JVPIQ https://www.mouser.co.uk/ProductDetail/Winbond/W25Q128JVPIQ?qs=qSfuJ%252Bfl%2Fd676hAD%252B1JSfw%3D%3D
1 | XKB7070-Z | XKB7070-Z | XKB7070-Z | SW1
1 | XT_30 | XT_30 | XT_30 | J2

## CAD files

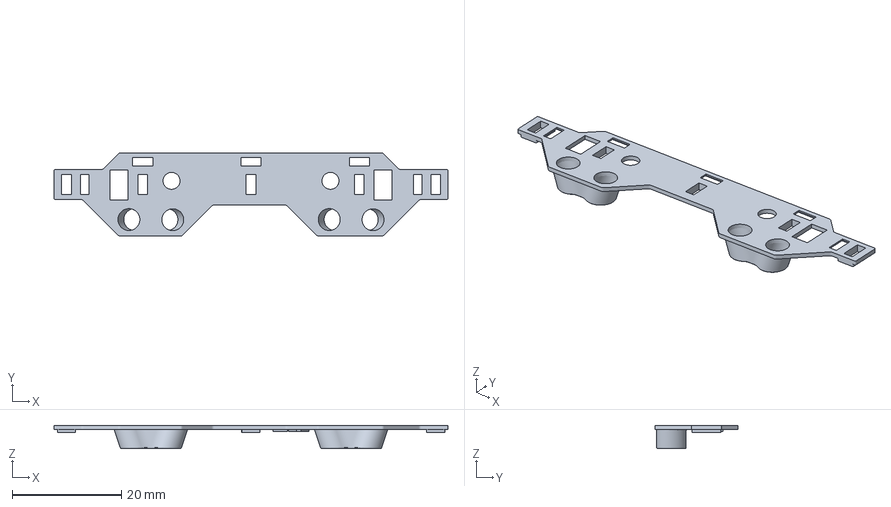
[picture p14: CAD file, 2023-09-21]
Hardware/Chassis and 3D models/Lightprotection V2.3mf
72.0 x 15.2 x 4.25 mm

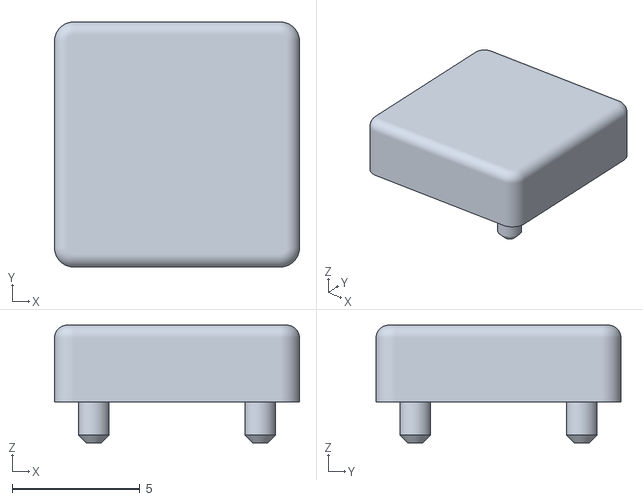
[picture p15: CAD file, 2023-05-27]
Hardware/Chassis and 3D models/Gyro Protection.stl
9.57 x 9.57 x 4.60

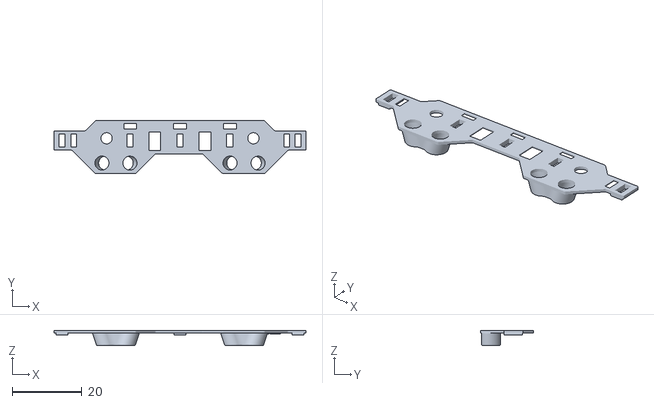
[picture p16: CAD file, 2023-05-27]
Hardware/Chassis and 3D models/Lightprotection V1.stl
72.0 x 15.2 x 4.25

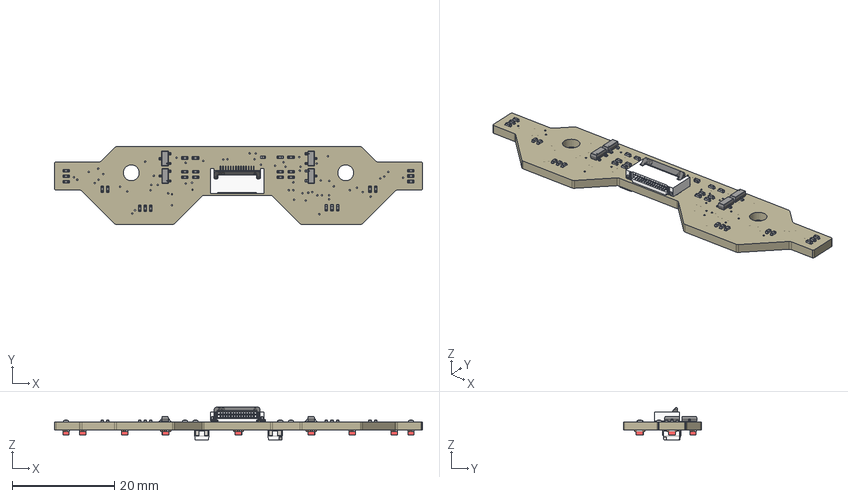
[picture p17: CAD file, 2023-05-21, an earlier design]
Hardware/RoboCore light sensor bar V1/RoboCore light sensor bar V1.step
72.0 x 15.2 x 6.41 mm
Board
FC05-S14FCT-00
CHIP-LED0805 x 7
RGBLED x 2
PinsArrayL x 4
FilletPinR x 4
base
Lötende x 2
Pins x 28
Cover x 28

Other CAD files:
Hardware/RoboCore light sensor bar V2/Lightsensor protection V2.step
Hardware/RGB Sensor V1/RoboCore RGB Sensor v1.f3d
Hardware/RoboCore light sensor bar V1/RoboCore light sensor bar V1.f3z
Hardware/RoboCore light sensor bar V2/RoboCore Light sensor bar v1.f3d

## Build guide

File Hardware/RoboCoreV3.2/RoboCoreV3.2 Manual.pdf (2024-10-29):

1

# RoboCoreV3.2 Manual

## Pinout

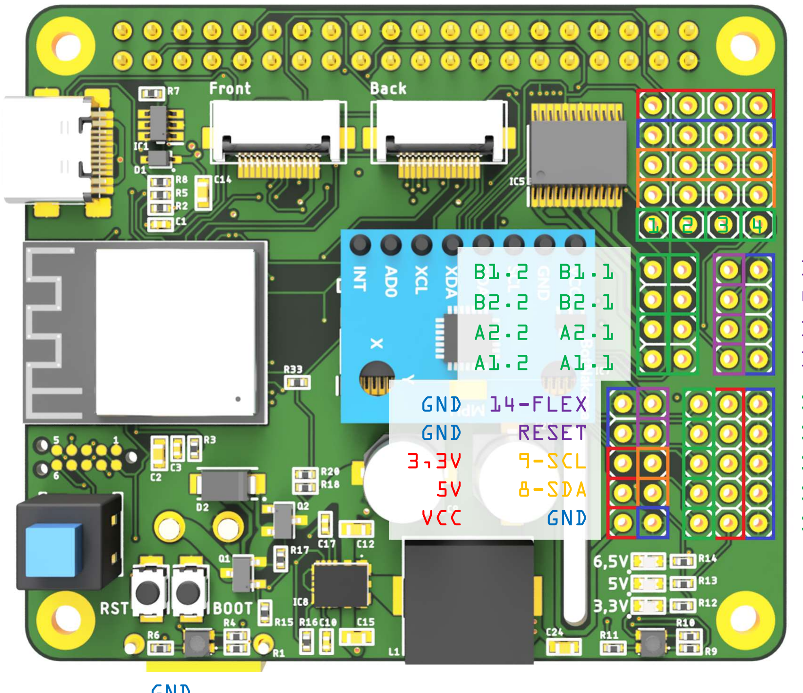
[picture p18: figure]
GND 14-FLEX; GND; RESET; 9-SCL; 8-SDA; VCC

Voltage
GND/Zero potential
Communication protocol
Digital output
Analog/Digital input

3,3V
GND
9-SCL
8-SDA
XSHT
18-T_L GND
41-T_M
17-T_R
16-T_E

GND
2S 8,4V

SVO5 5V GND
SVO4
SVO3
SVO2
SVO1

2

## Warning before use!

- If high power batteries are used, a large capacitor must be installed at the input!
- After powering up the RoboCore, always make sure that nothing is connected to the wrong pins. Always use the pinout diagram each time you change pins!
- Whenever the system is re-plugged or modified, ensure that the battery is always disconnected. Otherwise short circuits may occur on the PCB!

## Download Mode

If no program can be uploaded to the ESP32-S3, it must be set to download mode. The following steps are necessary
to do this:

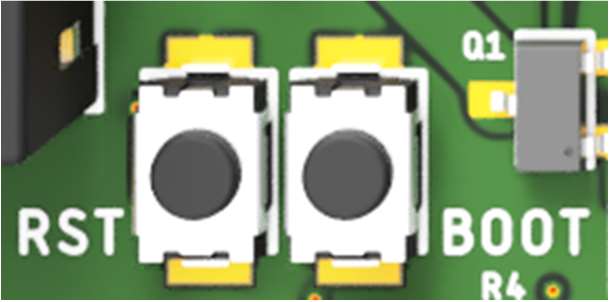
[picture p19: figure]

### 1. Press and hold the BOOT and RESET button 2. Connect the RoboCore to the computer via USB 3. Release the RESET button while still holding the BOOT button 4. Release the BOOT button after a few seconds

## Motor Connection

Use the following wiring diagram to connect the motors:

## Pinout

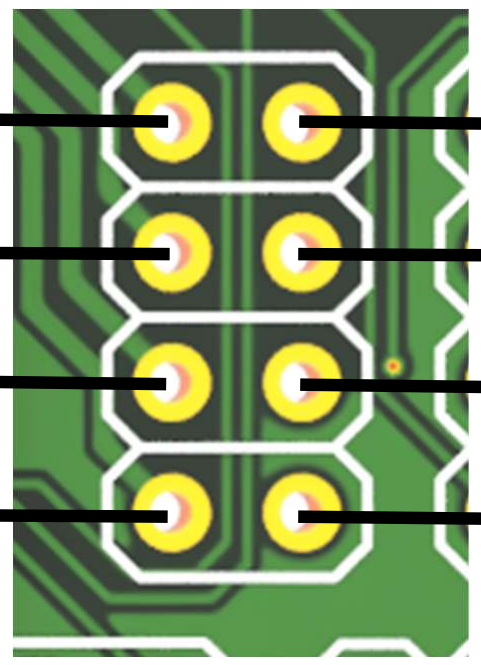
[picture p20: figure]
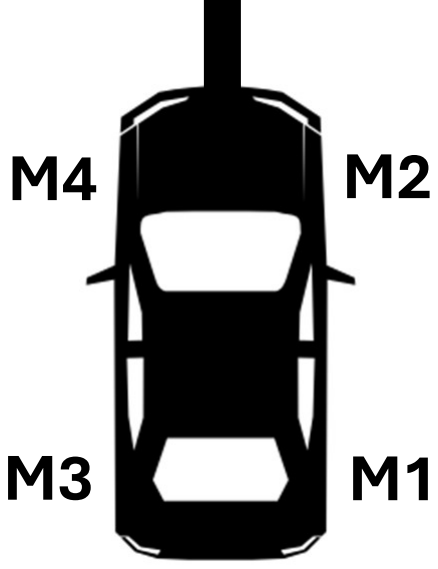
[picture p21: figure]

ESP32 GPIO | Pin name | Description
1 | 1-PT_REF_L | Reflection sensor left.
2 | 2-PT_L_1 | Light sensor left outside.
4 | 4-PT_L_0 | Light sensor left inside.
5 | 5-PT_R_0 | Light sensor right inside.
6 | 6-PT_R_1 | Light sensor right outside.

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
7 7 | -PT_REF_R | Reflection sensor right.
8 | 8-SDA 9-SCL | Data lines for I2C. 9 Data lines for I2C.
10 | 10-PT_L_3 | Light sensor left outside.
11 | 11-PT_L_2 | Light sensor left inside.
12 12 | -PT_R_2 | Light sensor right inside .
13 | 13-PT_R_3 | Light sensor right outside .
14 | 14-FLEX | A Flex sensor can be read out here .
15 | 15-VBAT | The battery voltage can be measured with this pin.
16 | 16-T_E | An input pull-up must be defined in the software! Buttons can be connected to this pin. LOW = pressed
17 | 17-T_R | An input pull-up must be defined in the software! Buttons can be connected to this pin. LOW = pressed
18 | 18-T_L | An input pull-up must be defined in the software! Buttons can be connected to this pin. LOW = pressed
21 | 21-PWMA1 | This pin determines the motor speed.
33 | 33-PWMA2 | This pin determines the motor speed.
34 | 34-PWMB1 | This pin determines the motor speed.
35 | 35-PWMB2 | This pin determines the motor speed.
36 | 36-WHITE_L | Light sensor strip LED white left. HIGH = ON
37 | 37-WHITE_R | Light sensor strip LED white right. HIGH = ON
38 | 38-WHITE | Light sensor strip LED white. HIGH = ON
39 | 39-RED | Light sensor strip LED red. HIGH = ON
40 | 40-GREEN | Light sensor strip LED green. HIGH = ON
41 | 41-T_M | An input pull-up must be defined in the software! Buttons can be connected to this pin. LOW = pressed
42 | 42-DS | New data enters the register.
47 | 47-STCP | Latches shifted data into output registers.
48 | 48-SHCP | Controls data shifting within the register.

4

Shiftregister GPIO | Pin Name | Description
Q0,0 | AIN1.1 | Determines the motor direction.
Q1,0 | AIN2.1 | Determines the motor direction.
Q2,0 | BIN1.1 | Determines the motor direction.
Q3,0 | BIN2.1 | Determines the motor direction.
Q4,0 | AIN1.2 | Determines the motor direction.
Q5,0 | AIN2.2 | Determines the motor direction.
Q6,0 | BIN1.2 | Determines the motor direction.
Q7,0 | BIN2.2 | Determines the motor direction.
Q0,1 | STBY1 | If the pin is set LOW, the motor driver is off and at HIGH it is on.
Q1.1 | STBY2 | If the pin is set LOW, the motor driver is off and at HIGH it is on.
Q2,1 | XSHT1 | A HIGH activates the TOF sensor.
Q3,1 | XSHT2 | A HIGH activates the TOF sensor.
Q4,1 | XSHT3 | A HIGH activates the TOF sensor.
Q5,1 | XSHT4 | A HIGH activates the TOF sensor.
Q6,1 | Q6 | External digital pin.
Q7,1 | Q7 | External digital pin.
PWM Bus | Pin Name | Description
CH0 | SVO1 | A servo can be connected to this pin.
CH1 | SVO2 | A servo can be connected to this pin.
CH2 | SVO3 | A servo can be connected to this pin.
CH3 | SVO4 | A servo can be connected to this pin.
CH4 | SVO5 | A servo can be connected to this pin.
CH5 | CH5 | External PWM pin.
CH6 | CH6 | External PWM pin.
CH7 | CH7 | External PWM pin.

5

CH8 | RED_L | RoboCore RGB red left, PWM inverted! 255 = OFF, 0 = ON
CH9 | GREEN_L | RoboCore RGB green left, PWM inverted! 255 = OFF, 0 = ON
CH10 | BLUE_L | RoboCore RGB blue left, PWM inverted! 255 = OFF, 0 = ON
CH11 | RED_R | RoboCore RGB red right, PWM inverted! 255 = OFF, 0 = ON
CH12 | GREEN_R | RoboCore RGB green right, PWM inverted! 255 = OFF, 0 = ON
CH13 | BLUE_R | RoboCore RGB blue right, PWM inverted! 255 = OFF, 0 = ON
GPIO | Input | Output | Pin assignment | Note | Arduino pinMode() 0 | NO | NO | 0-STAT
Strapping Pin, Responsible for boot
configuration, BOOT 3 | YES | YES | /
Strapping Pin, JTAG, ADC 12Bit (4096), RTC, TOUCH3
45 | YES | YES | / | Strapping Pin, VSPI 46 | YES | YES | /
Strapping Pin, use no pullup or pulldown resistor, LOG
43 | YES | YES | TXD0 | TXD0
44 | YES | YES | RXD0 | RXD0
1 | YES | YES | 1-PT_REF_L | ADC 12Bit (4096), RTC, TOUCH
2 | YES | YES | 2-PT_L_1 | ADC 12Bit (4096), RTC, TOUCH
4 | YES | YES | 4-PT_L_0 | ADC 12Bit (4096), RTC, TOUCH
5 | YES | YES | 5-PT_R_0 | ADC 12Bit (4096), RTC, TOUCH
6 | YES | YES | 6-PT_R_1 | ADC 12Bit (4096), RTC, TOUCH
7 | YES | YES | 7-PT_REF_R | ADC 12Bit (4096), RTC, TOUCH
8 | YES | YES | 8-SDA | SDA, ADC 12Bit (4096), RTC, TOUCH
9 | YES | YES | 9-SCL | SCL, ADC 12Bit (4096), RTC, TOUCH
10 | YES | YES | 10-PT_L_3 | SPI3_CS, ADC 12Bit (4096), RTC, TOUCH
11 | YES | YES | 11-PT_L_2 | SPI3_MOSI, ADC 12Bit (4096), RTC, TOUCH
12 | YES | YES | 12-PT_R_2 | SPI3_CLK, ADC 12Bit (4096), RTC, TOUCH
13 | YES | YES | 13-PT_R_3 | SPI3_MISO, ADC 12Bit (4096), RTC, TOUCH
14 | YES | YES | 14-FLEX | ADC 12Bit (4096), RTC, TOUCH
15 | YES | YES | 15-VBAT | ADC 12Bit (4096), RTC
16 | YES | YES | 16-T_E | ADC 12Bit (4096), RTC | INPUT_PULLUP
17 | YES | YES | 17-T_R | ADC 12Bit (4096), RTC | INPUT_PULLUP
18 | YES | YES | 18-T_L | ADC 12Bit (4096), RTC | INPUT_PULLUP
19 | YES | YES | D- | D-, ADC 12Bit (4096), RTC
20 | YES | YES | D+ | D+, ADC 12Bit (4096), RTC
21 | YES | YES | 21-PWMA1 | RTC
26 | YES | YES | / 33 | YES | YES | 33-PWMA2
34 | YES | YES | 34-PWMB1
35 | YES | YES | 35-PWMB2 | SPI2_MOSI 36 | YES | YES | 36-WHITE_L | SPI2_CLK | HIGH = ON
37 | YES | YES | 37-WHITE_R | SPI2_MISO | HIGH = ON
38 | YES | YES | 38-WHITE | HIGH = ON
39 | YES | YES | 39-RED | SPI2_CS | HIGH = ON
40 | YES | YES | 40-GREEN | HIGH = ON
41 | YES | YES | 41-T_M | INPUT_PULLUP
42 | YES | YES | 42-DS 47 | YES | YES | 47-STCP
48 | YES | YES | 48-SHCP

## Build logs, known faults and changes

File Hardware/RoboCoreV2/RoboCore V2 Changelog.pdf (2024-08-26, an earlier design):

# RoboCore V1->V2 Changelog

If the RoboCore V1 PCB was used for the program and you now want to change from the V1 to the V2, you must ensure that you change the following settings in the program:

ESP32 GPIO:

1. Pin 13 (13-S3) → 13-SERVO5
2. Pin 14 (14-T_R) → 14-S3
3. Pin 15 (15-ENC_SW) → pinMode(15, INPUT_PULLUP)
4. Pin 15 (15-ENC_SW) → Pressing the encoder button sets the pin to LOW, previously it was HIGH on the V1!
5. Pin 23 (23-PWMA) → 23-T_R
6. Pin 23 → pinMode(23, INPUT_PULLUP)
7. Pin 26 (26-METAL_S) → 26-PWMA

Multiplexer GPIO:

1. I8 (AE1) → I13
2. I9 (AE2) → I14
3. I10 (AE3) → I15 This pin is normally connected to MPU6050 Interupt. This can be deactivated via a jumper
4. Pin 26 (26-METAL_S) → I12

Shiftregister:

1. Q5,0 (PT_WHITE) → LED_L_RED
2. Q6,0 (PT_RED) → LED_L_GREEN
3. Q7,0 (PT_GREEN) → LED_L_BLUE
4. Q0,1 (PT_BLUE) → LED_R_RED
5. Q1,1 (LED_L_RED) → LED_R_GREEN
6. Q2,1 (LED_L_GREEN) → LED_R_BLUE
7. Q3,1 (LED_L_BLUE) → XSHT1
8. Q4,1 (LED_R_RED) → XSHT2
9. Q5,1 (LED_R_GREEN) → XSHT3
10. Q6,1 (LED_R_BLUE) → XSHT4
11. Q7,1 (XSHT1) → RGB_RED
12. Q0,2 (XSHT2) → RGB_GREEN
13. Q1,2 (XSHT3) → PT_WHITE
14. Q2,2 (XSHT4) → PT_RED
15. Q3,2 (DE1) → PT_GREEN
16. Q4,2 (DE2) → PT_BLUE
17. Q5,2 (DE3) → DE1
18. DE2 → Q6,2
19. DE3 → Q7,2

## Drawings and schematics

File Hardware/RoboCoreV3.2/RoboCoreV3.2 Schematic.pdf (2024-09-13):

Sheet: ABCDE | 1 | 2 | 3 | 4 | 5 | 6 | 7 | 8 | ABCDE 1 | 2 | 3 | 4 | 5 | 6 | 7 | 8

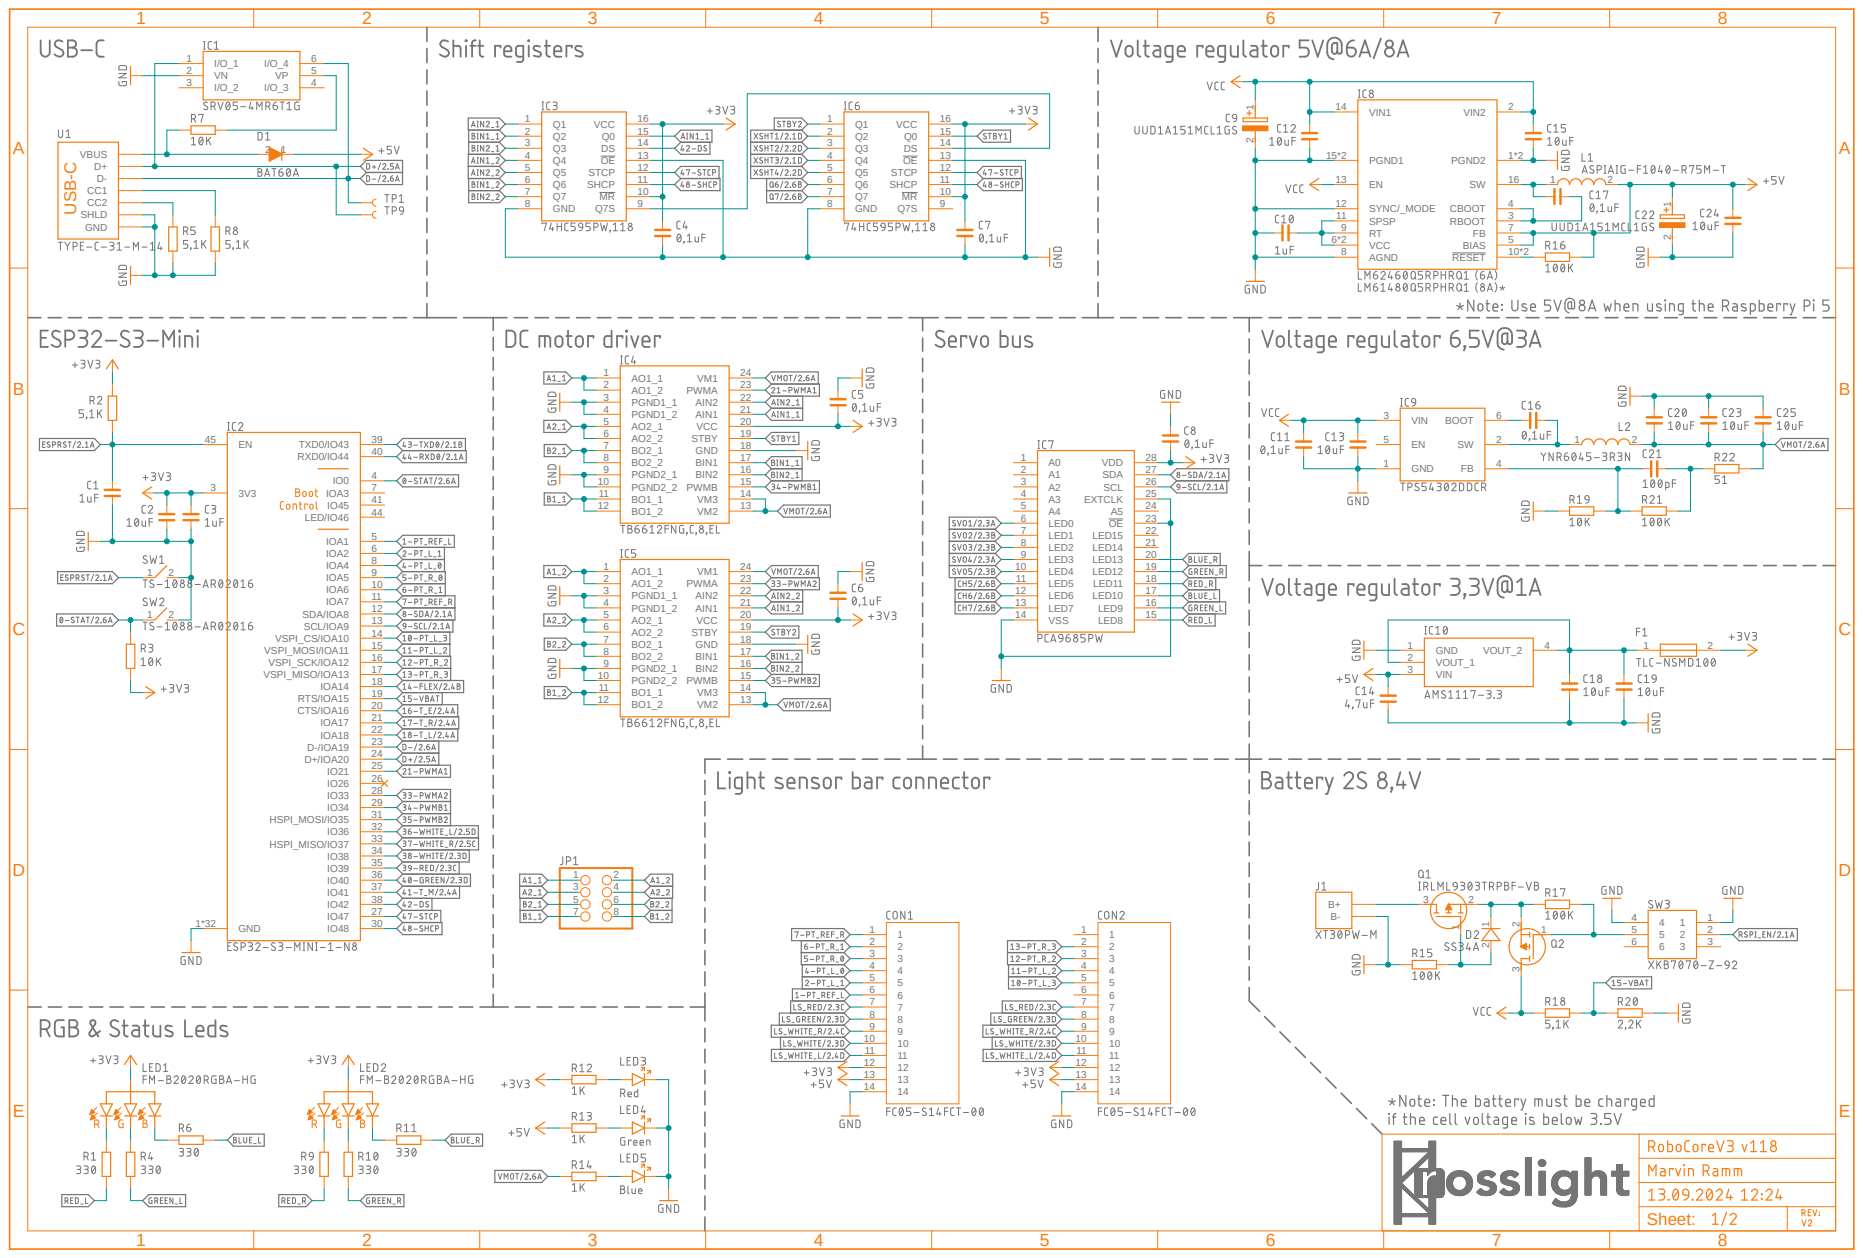
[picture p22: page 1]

7 | 8 1 2 | 3 1 2 | 3 | 1 2 | 3 1 2 | 3 | 1 2 | 3 | Sheet: ABCD | 1 | 2 | 3 | 4 | 5 | 6 | ABCD 1 | 2 | 3 | 4 | 5 | 6

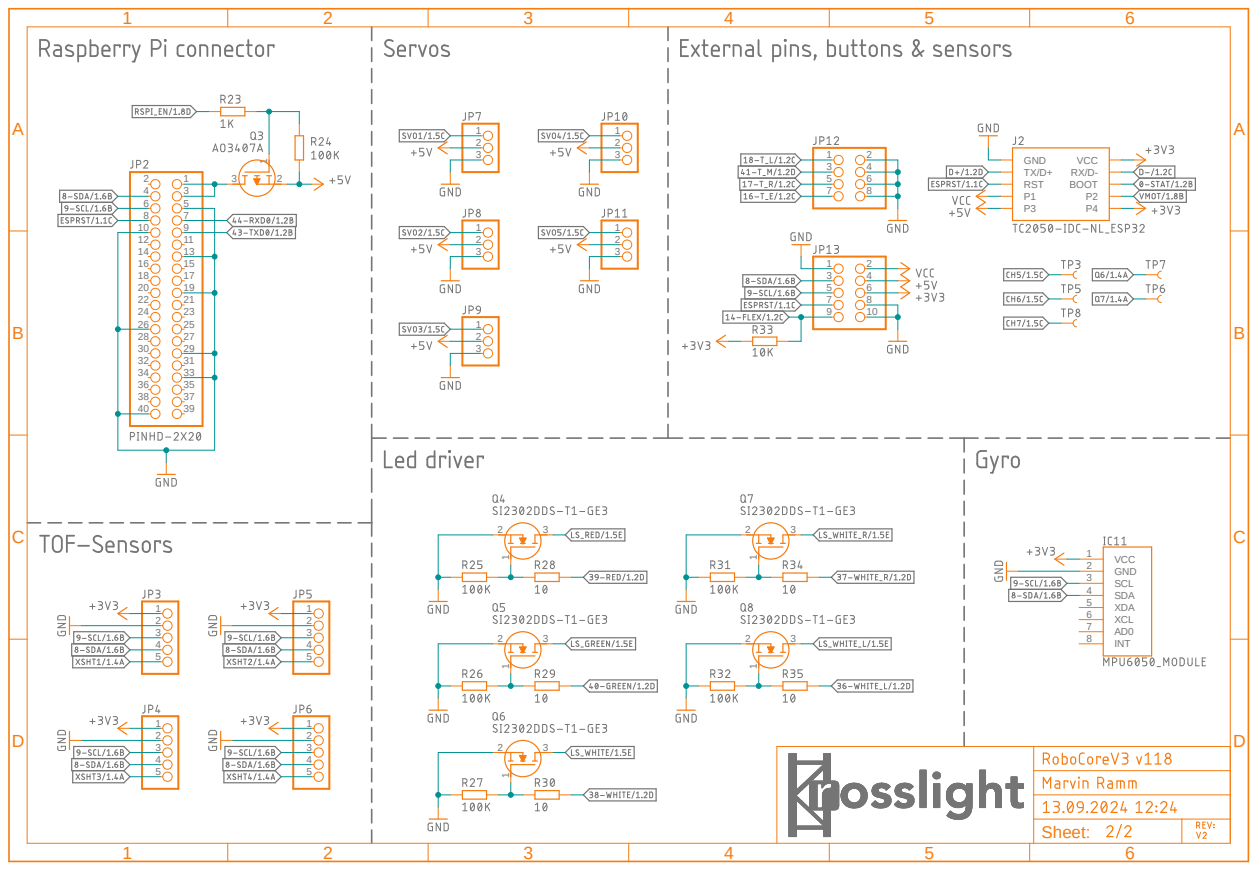
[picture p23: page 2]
SDA 4; XDA 5; XCL 6; VCC 1; GND 2; SCL 3; INT 8 12345; GND; TX/D+ RST P1P3; VCC; RX/D- BOOTP2P4 2

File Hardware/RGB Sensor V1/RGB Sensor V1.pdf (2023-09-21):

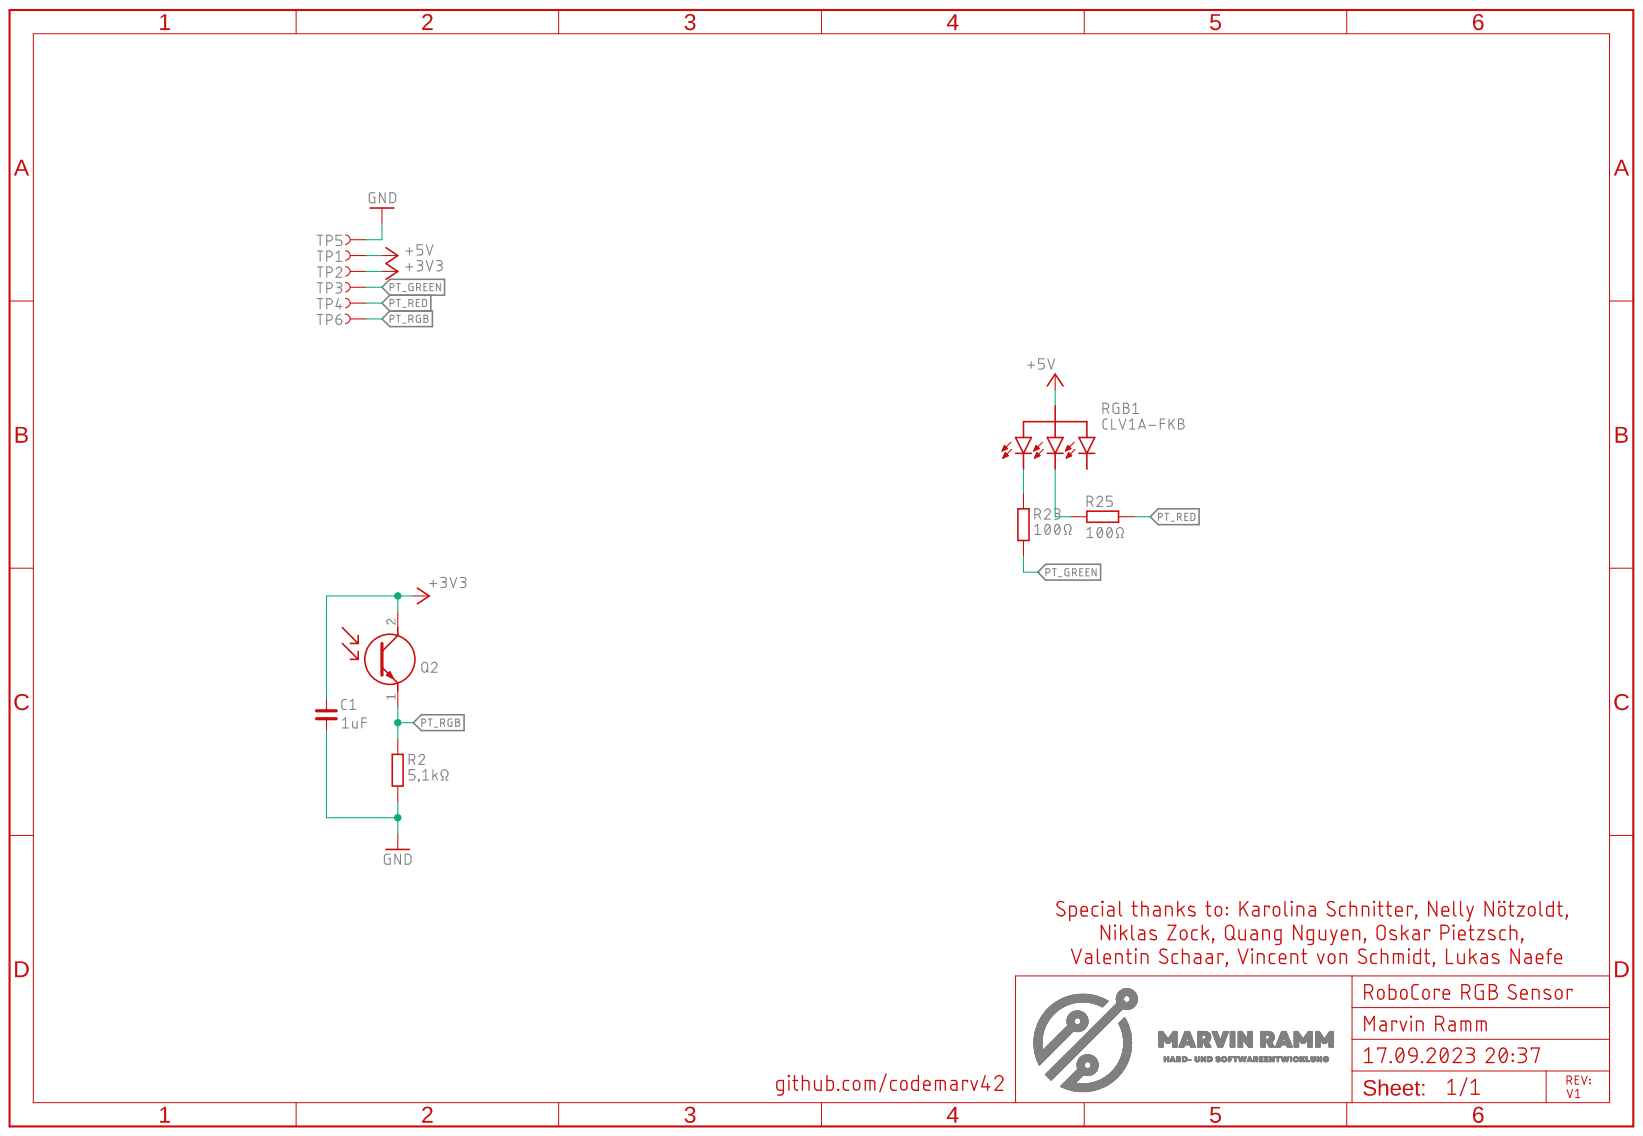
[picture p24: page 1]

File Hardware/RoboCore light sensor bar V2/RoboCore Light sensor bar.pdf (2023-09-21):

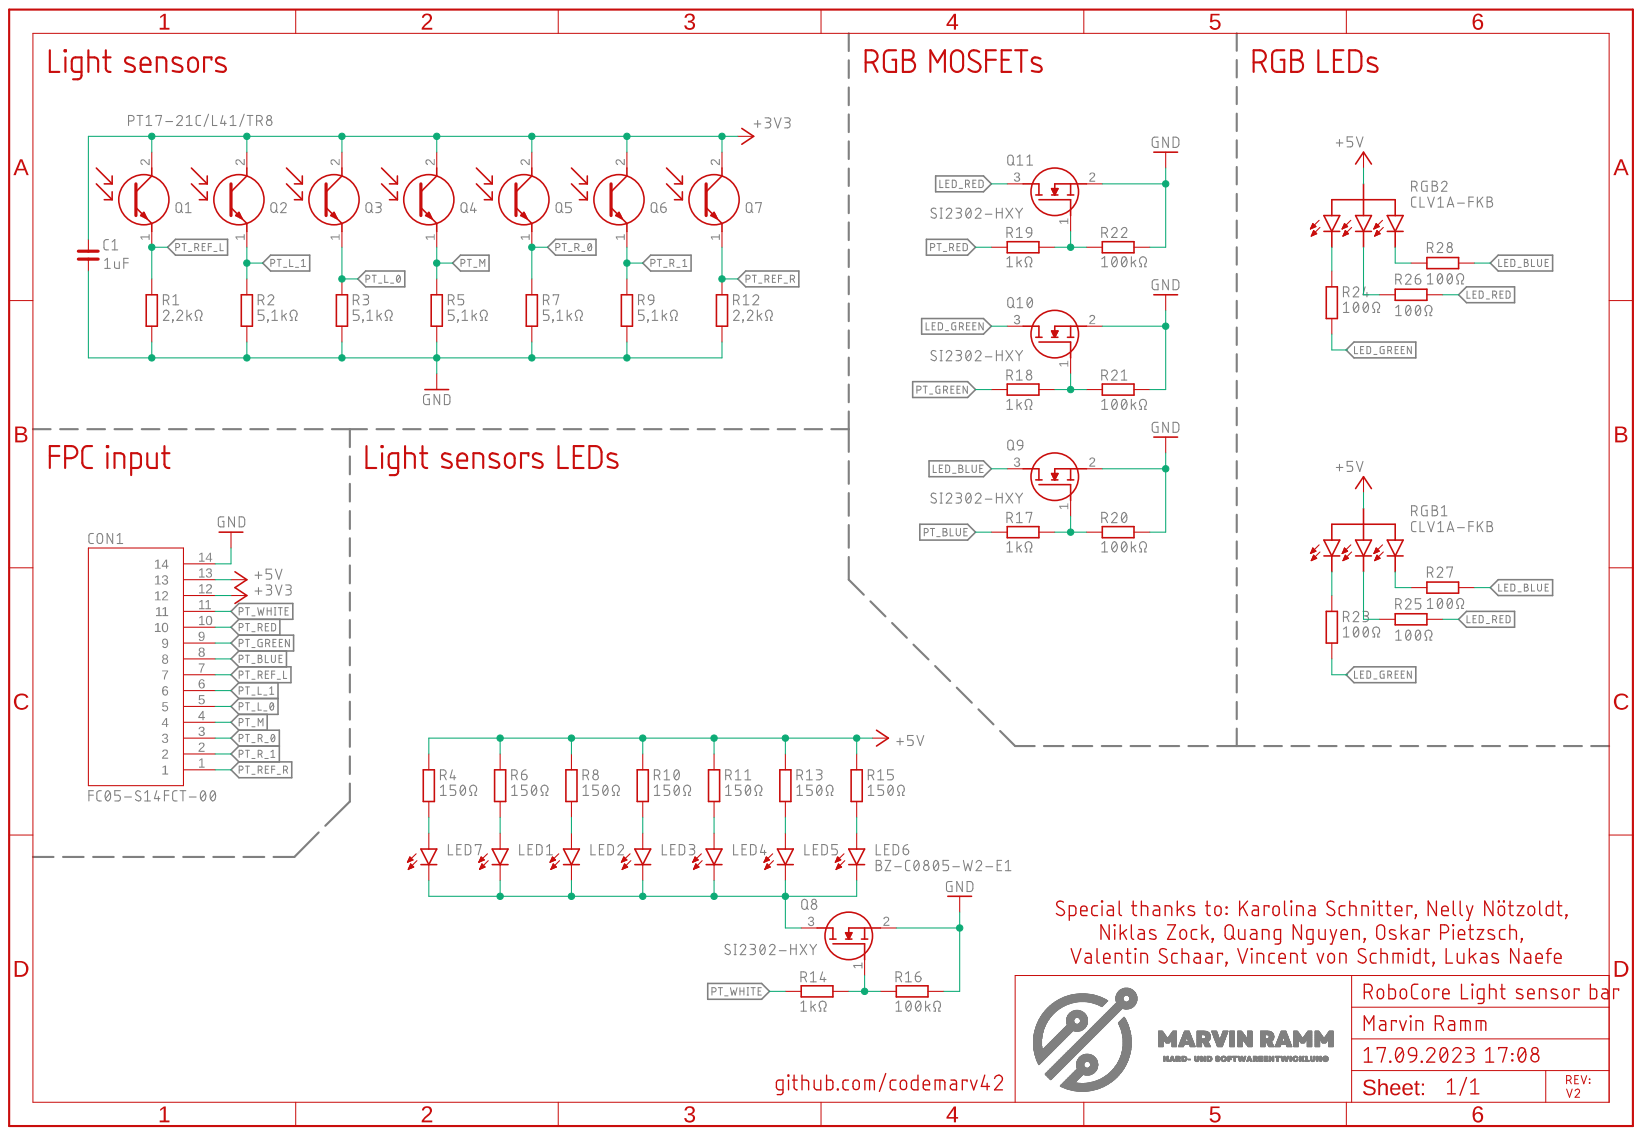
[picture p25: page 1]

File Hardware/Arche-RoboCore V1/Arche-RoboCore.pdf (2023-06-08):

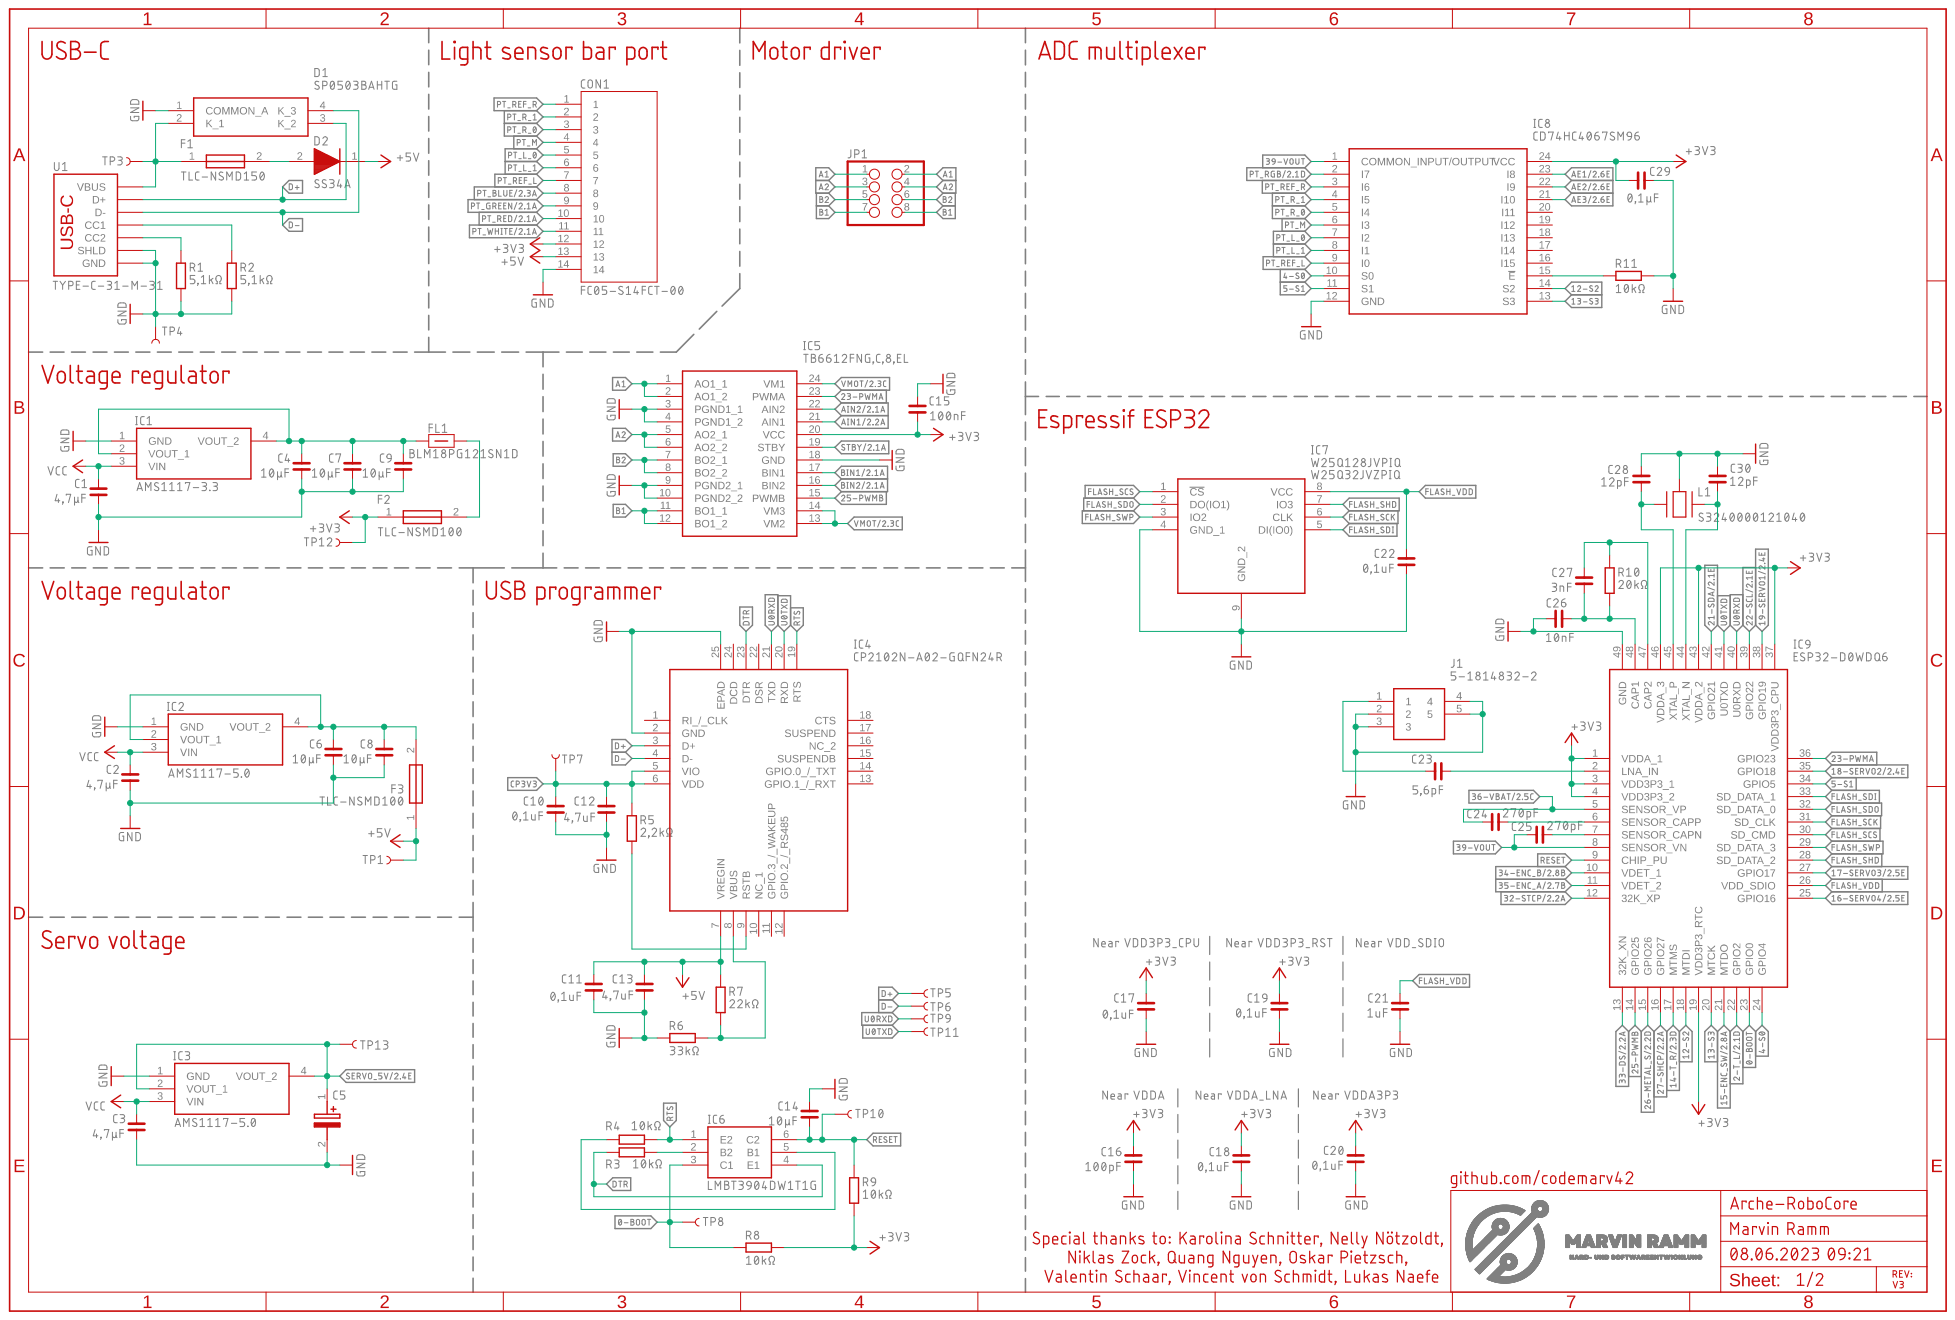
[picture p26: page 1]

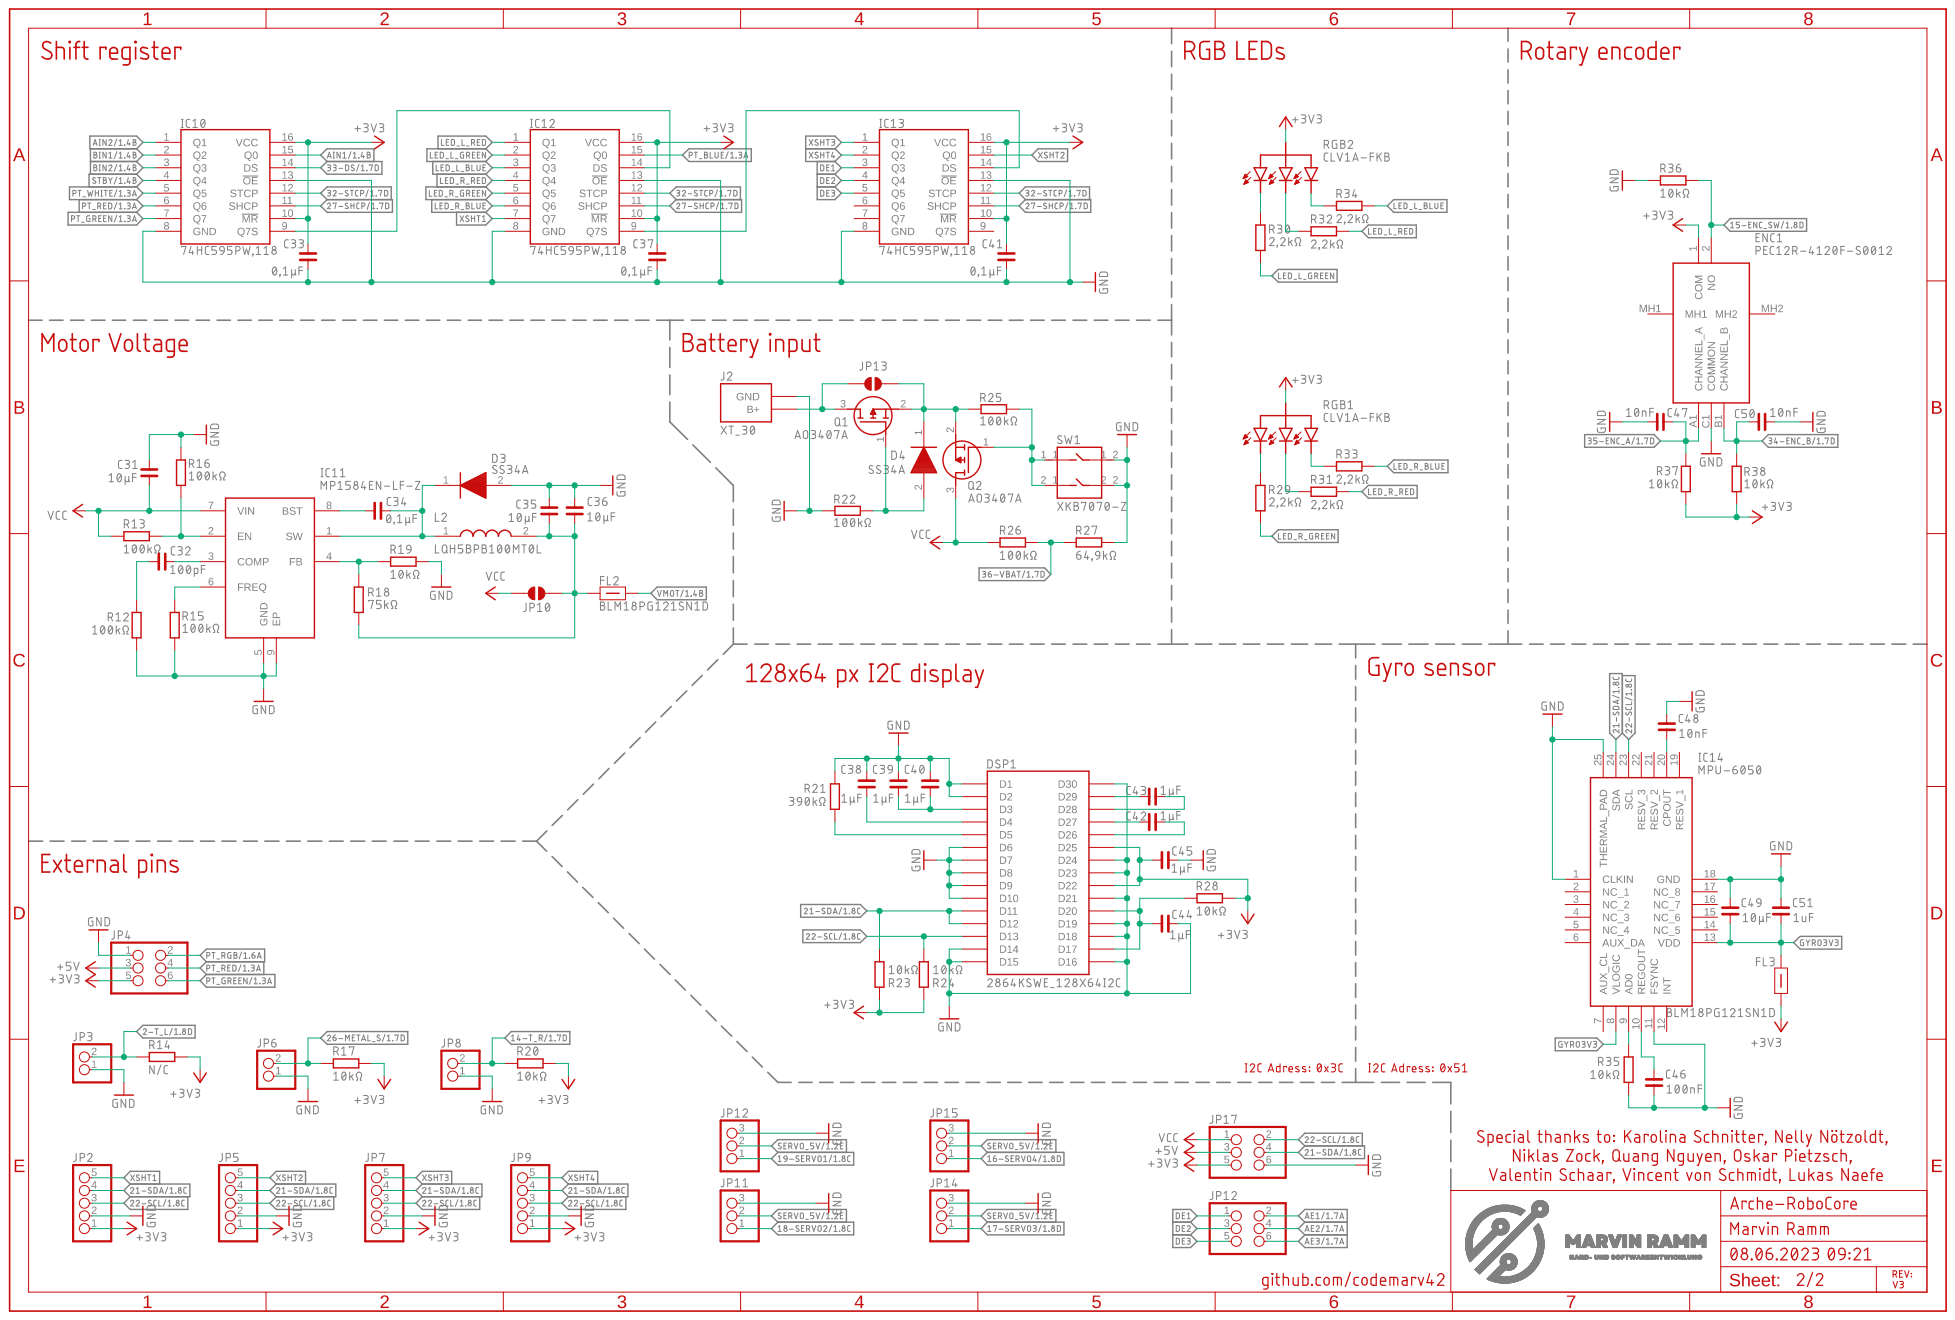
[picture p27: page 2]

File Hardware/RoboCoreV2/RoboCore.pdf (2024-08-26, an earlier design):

1 | 2 GND 1 | VOUT_1 2 | VIN 3 | VOUT_2 | 4 GND 1 | VOUT_1 2 | VIN 3 | VOUT_2 | 4 | 1 2 USB⁻C
Sheet: ABCDE | 1 | 2 | 3 | 4 | 5 | 6 | 7 | 8 | ABCDE 1 | 2 | 3 | 4 | 5 | 6 | 7 | 8

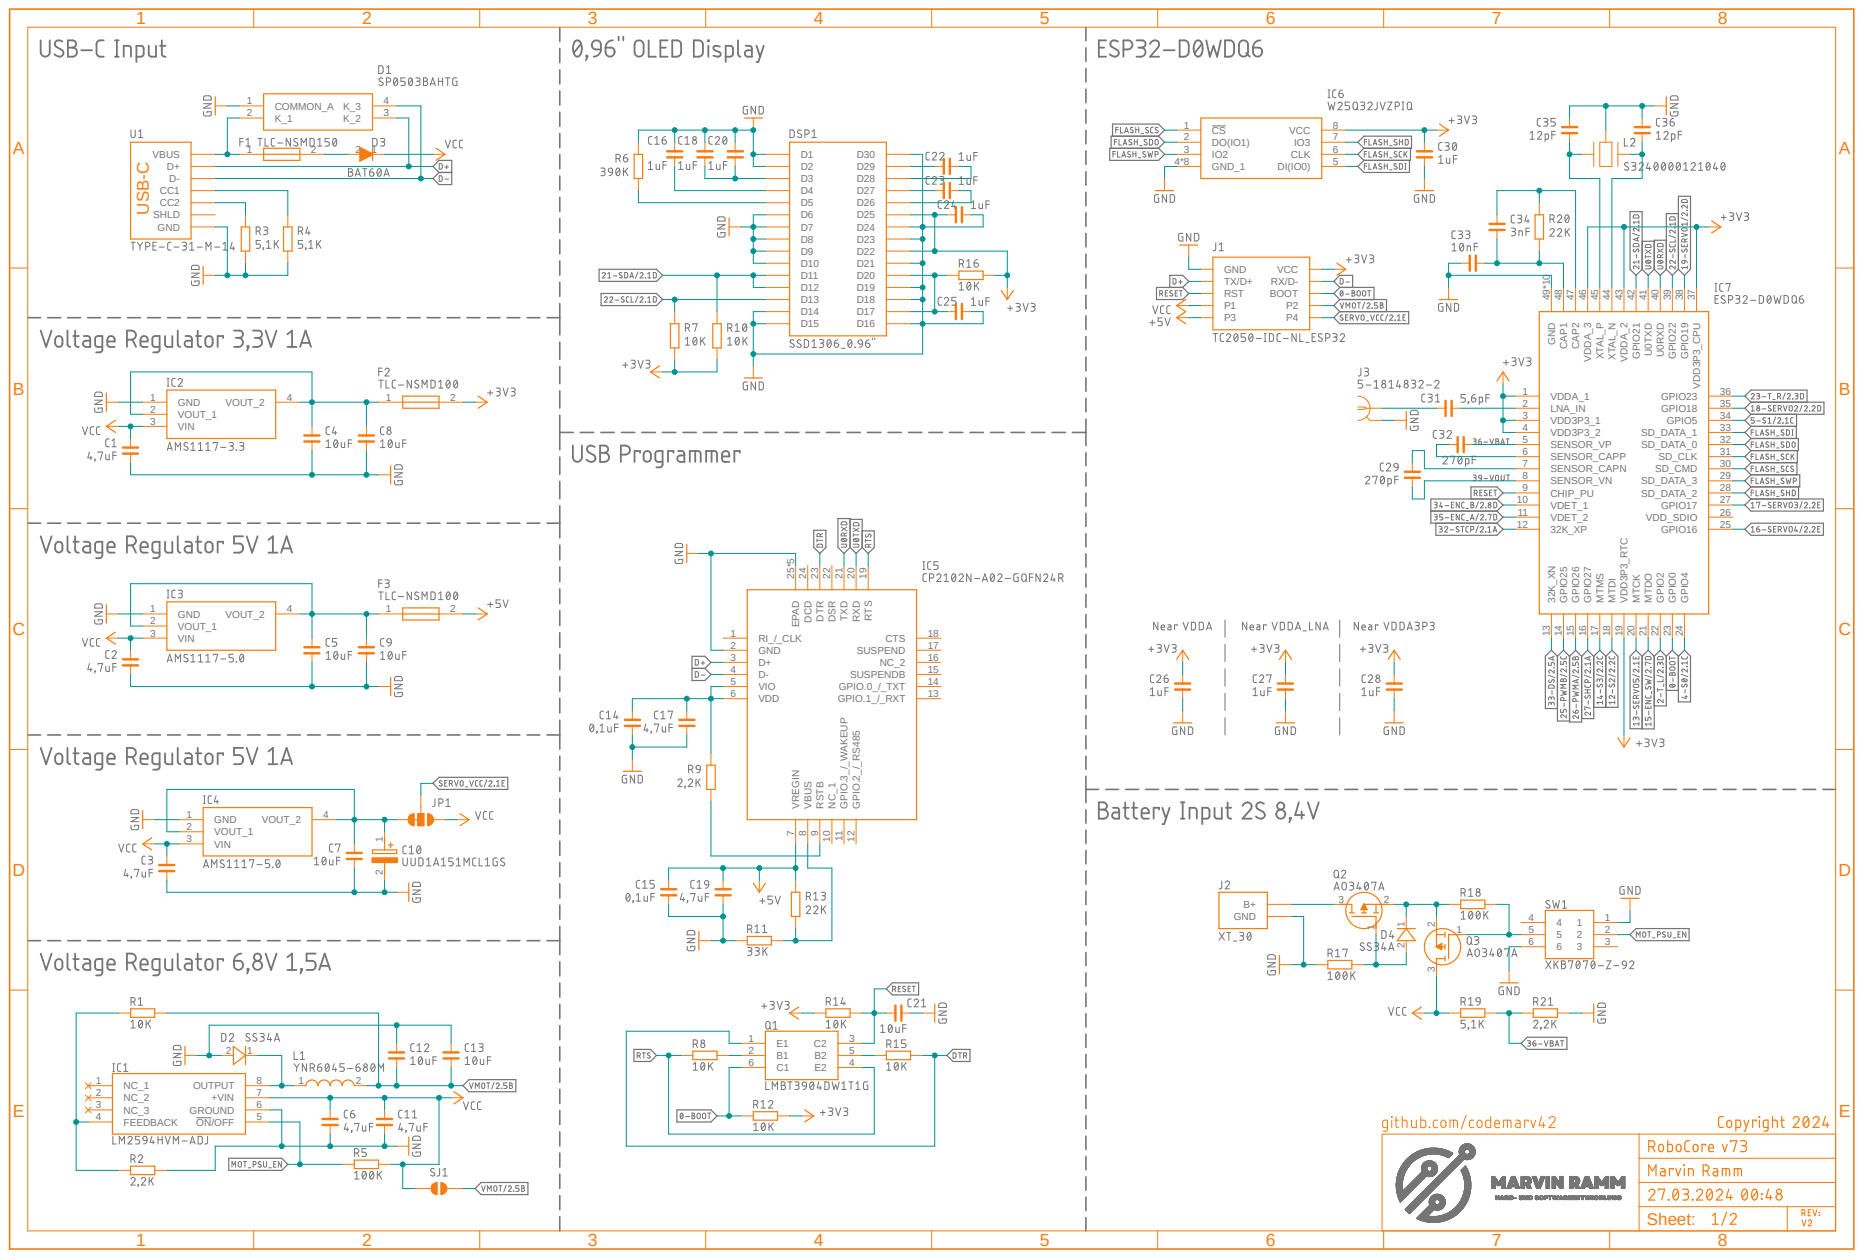
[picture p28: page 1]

25 GND ⁴⁹*10 CAP¹ ⁴⁸ CAP² ⁴⁷ VDDA_3 46 XTAL_P ⁴⁵ XTAL_N ⁴⁴ VDDA_2 43 GPIO²¹ ⁴² U⁰TXD ⁴¹ U⁰RXD ⁴⁰ GPIO²² ³⁹ GPIO¹⁹ ³⁸ VDD³P³_CPU ³⁷

15 S2 | 14 S3 | 13 1 1 | 2 2 | 3 3 | 4 4 | 5 5 | 6 6 | 7 7 | 8 8 | 9 9
Sheet: ABCDE | 1 | 2 | 3 | 4 | 5 | 6 | 7 | 8 | ABCDE 1 | 2 | 3 | 4 | 5 | 6 | 7 | 8

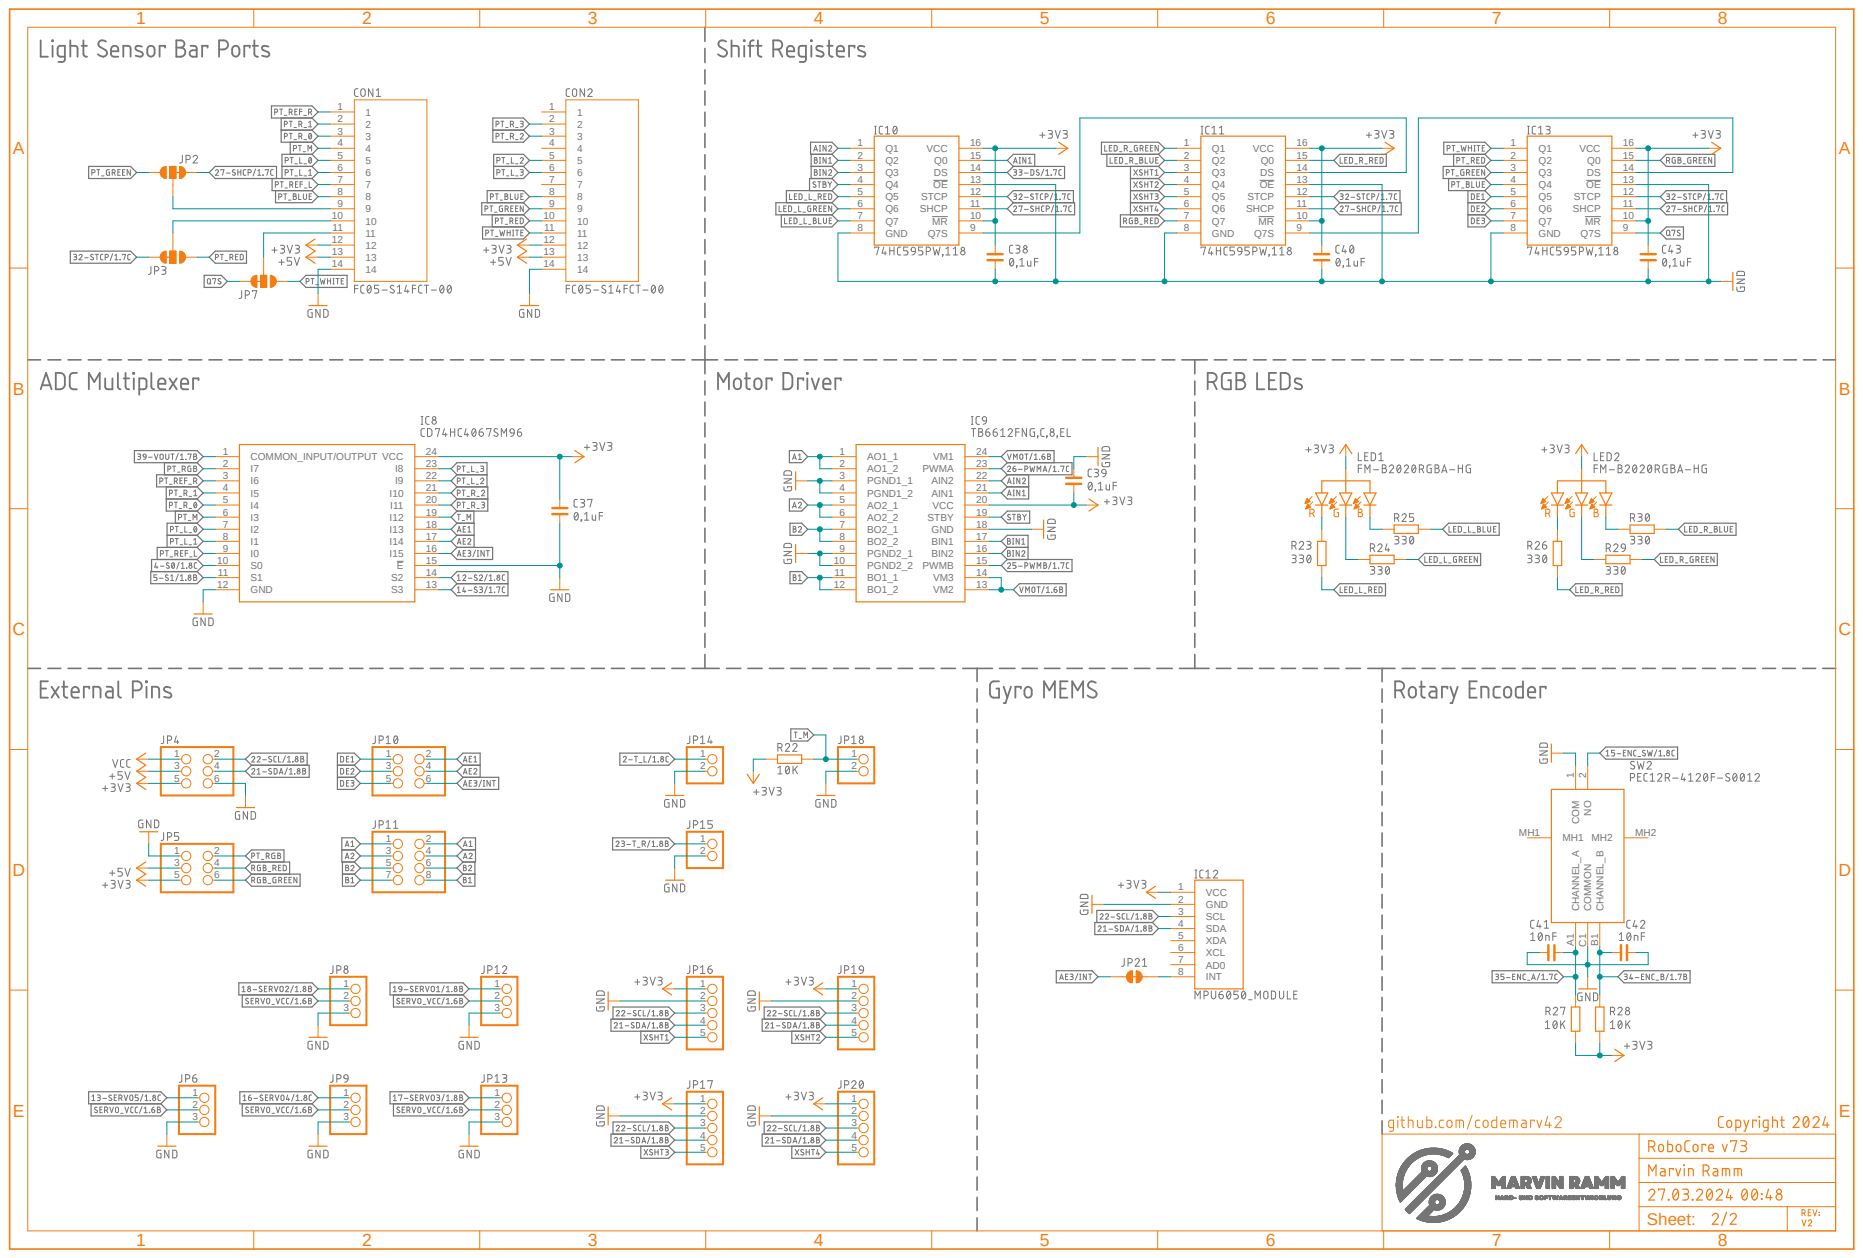
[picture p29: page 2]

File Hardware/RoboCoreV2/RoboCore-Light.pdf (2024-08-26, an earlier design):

9 | Sheet: ABCD | 1 | 2 | 3 | 4 | 5 | 6 | ABCD 1 | 2 | 3 | 4 | 5 | 6

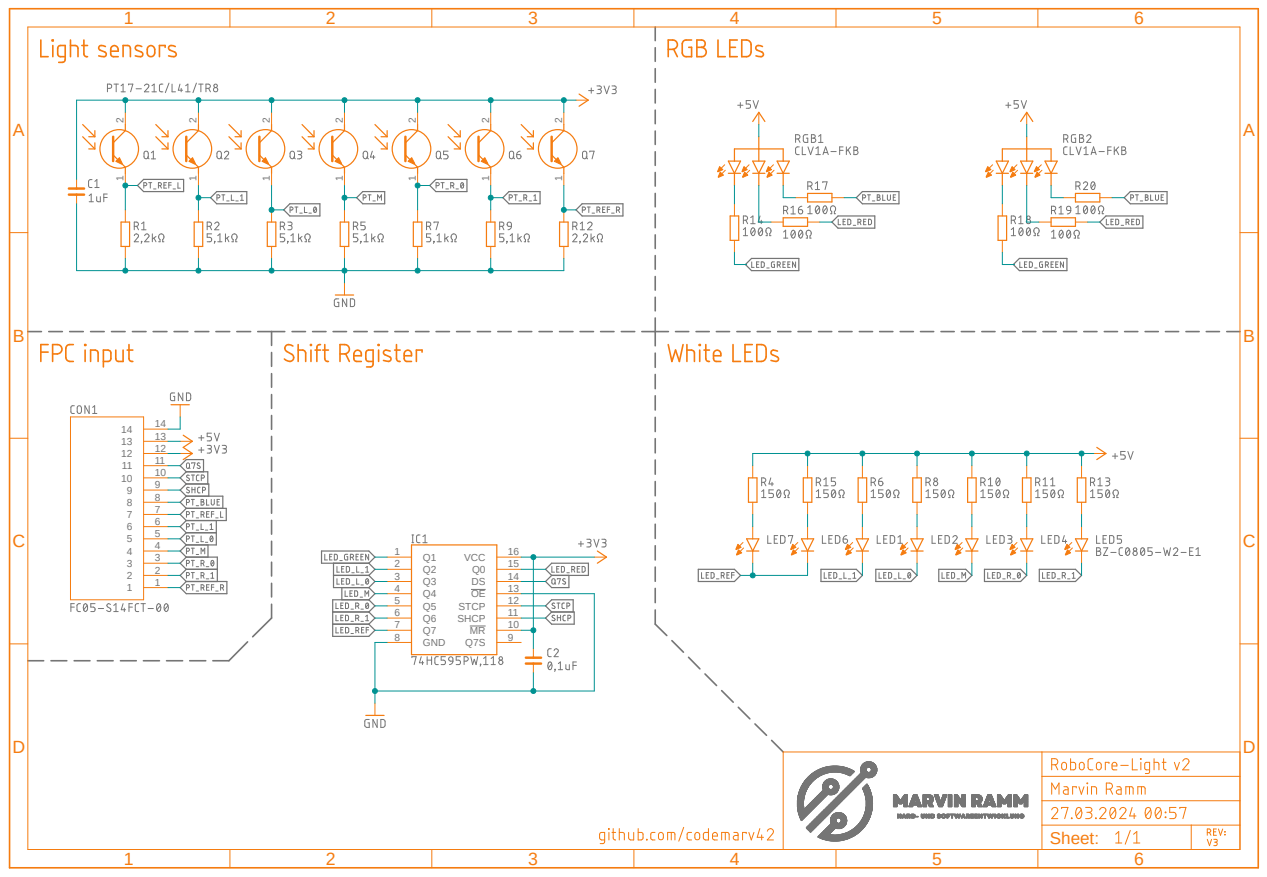
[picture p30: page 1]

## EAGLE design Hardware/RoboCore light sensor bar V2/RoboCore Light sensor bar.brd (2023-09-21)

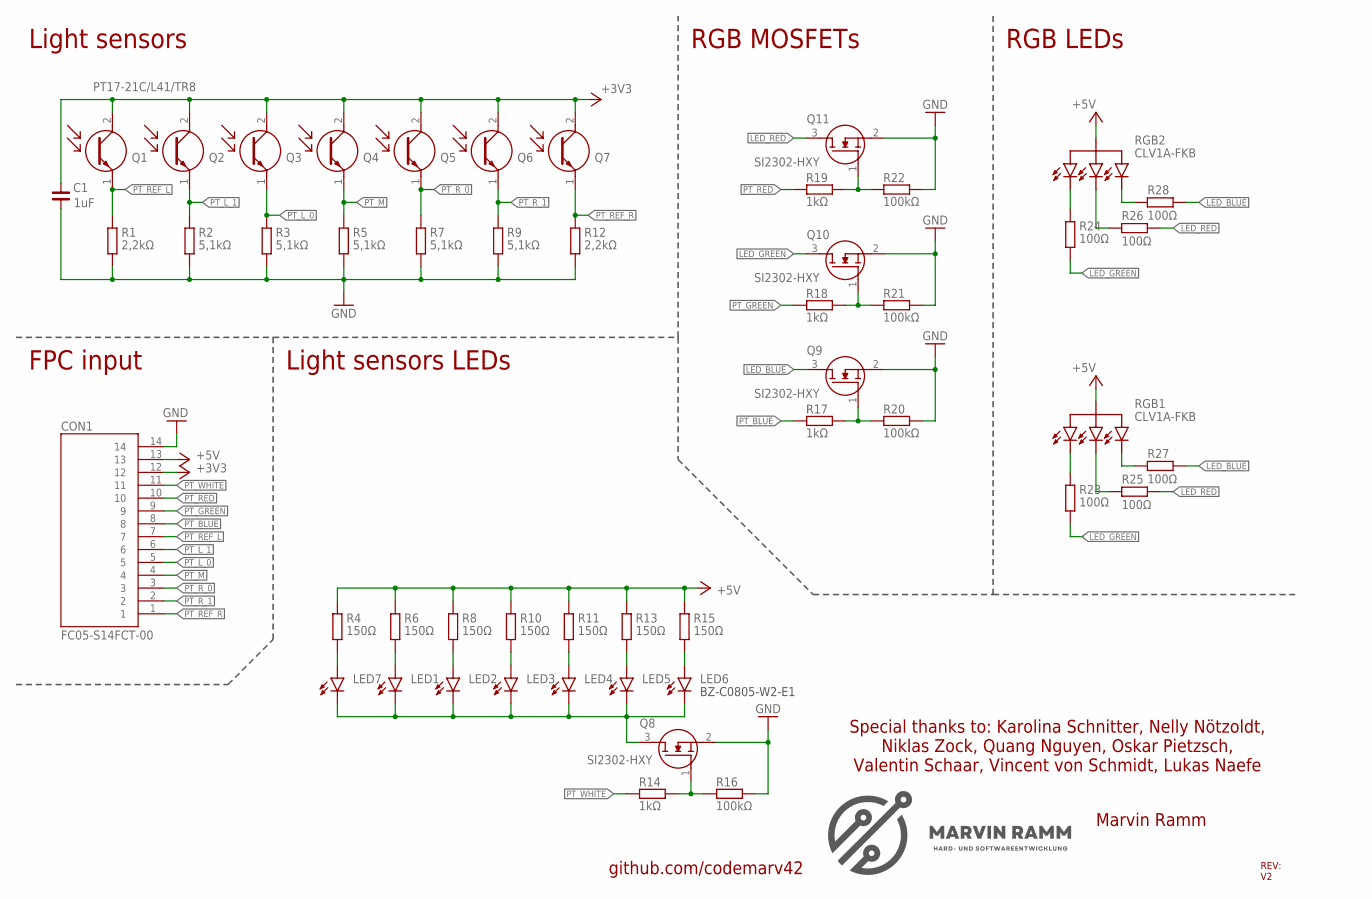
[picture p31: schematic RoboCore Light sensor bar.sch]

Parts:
C1: 1uF; C0402
CON1: FC05-S14FCT-00
LED1, LED2, LED3, LED4, LED5, LED6, LED7: LEDCHIP-LED0805; CHIP-LED0805
Q1, Q2, Q3, Q4, Q5, Q6, Q7: PT17-21C/L41/TR8; 0805
Q8, Q9, Q10, Q11: SI2302DDS-T1-GE3; SOT95P237X112-3N
R1, R12: 2,2kΩ; R0402
R2, R3, R5, R7, R9: 5,1kΩ; R0402
R4, R6, R8, R10, R11, R13, R15: 150Ω; R0402
R14, R17, R18, R19: 1kΩ; R0402
R16, R20, R21, R22: 100kΩ; R0402
R23, R24, R25, R26, R27, R28: 100Ω; R0402
RGB1, RGB2: RGBLED

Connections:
+3V3: C1.2, CON1.12, Q1.2 (C), Q2.2 (C), Q3.2 (C), Q4.2 (C), Q5.2 (C), Q6.2 (C), Q7.2 (C)
+5V: CON1.13, R4.1, R6.1, R8.1, R10.1, R11.1, R13.1, R15.1, RGB1.+5V, RGB2.+5V
GND: C1.1, CON1.14, Q8.2 (S), Q9.2 (S), Q10.2 (S), Q11.2 (S), R1.2, R2.2, R3.2, R5.2, R7.2, R9.2, R12.2, R16.2, R20.2, R21.2, R22.2
LED_BLUE: Q9.3 (D), R27.2, R28.2
LED_GREEN: Q10.3 (D), R23.2, R24.2
LED_RED: Q11.3 (D), R25.2, R26.2
unnamed: LED1.C, LED2.C, LED3.C, LED4.C, LED5.C, LED6.C, LED7.C, Q8.3 (D)
unnamed: LED7.A, R4.2
unnamed: Q11.1 (G), R19.2, R22.1
unnamed: Q10.1 (G), R18.2, R21.1
unnamed: Q9.1 (G), R17.2, R20.1
unnamed: LED5.A, R13.2
unnamed: LED6.A, R15.2
unnamed: Q8.1 (G), R14.2, R16.1
unnamed: LED4.A, R11.2
unnamed: R24.1, RGB2.P3
unnamed: R28.1, RGB2.P1
unnamed: R26.1, RGB2.P2
unnamed: R23.1, RGB1.P3
unnamed: R27.1, RGB1.P1
unnamed: R25.1, RGB1.P2
unnamed: LED3.A, R10.2
unnamed: LED2.A, R8.2
unnamed: LED1.A, R6.2
PT_BLUE: CON1.8, R17.1
PT_GREEN: CON1.9, R18.1
PT_L_0: CON1.5, Q3.1 (E), R3.1
PT_L_1: CON1.6, Q2.1 (E), R2.1
PT_M: CON1.4, Q4.1 (E), R5.1
PT_RED: CON1.10, R19.1
PT_REF_L: CON1.7, Q1.1 (E), R1.1
PT_REF_R: CON1.1, Q7.1 (E), R12.1
PT_R_0: CON1.3, Q5.1 (E), R7.1
PT_R_1: CON1.2, Q6.1 (E), R9.1
PT_WHITE: CON1.11, R14.1

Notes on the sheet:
Light sensors
RGB2
CLV1A-FKB
RGB1
Light sensors LEDs
SI2302-HXY
Marvin Ramm
REV: V2
github.com/codemarv42
FPC input
RGB MOSFETs
RGB LEDs
Special thanks to: Karolina Schnitter, Nelly Nötzoldt, Niklas Zock, Quang Nguyen, Oskar Pietzsch, Valentin Schaar, Vincent von Schmidt, Lukas Naefe
BZ-C0805-W2-E1

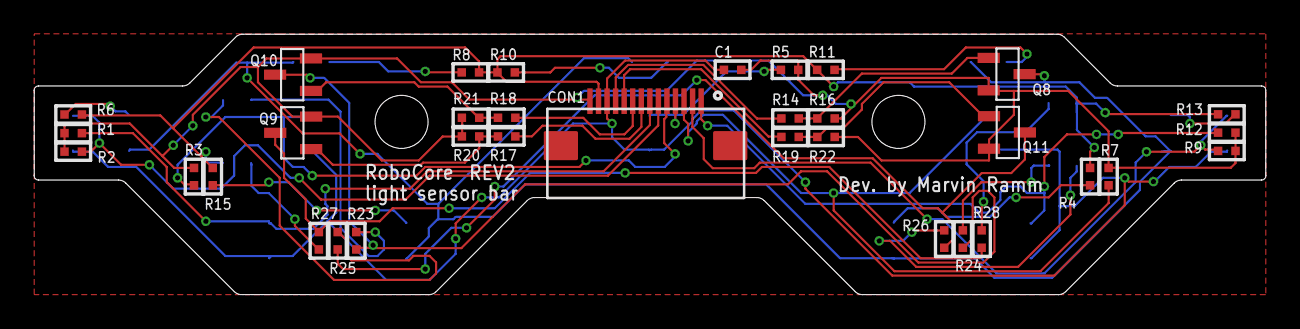
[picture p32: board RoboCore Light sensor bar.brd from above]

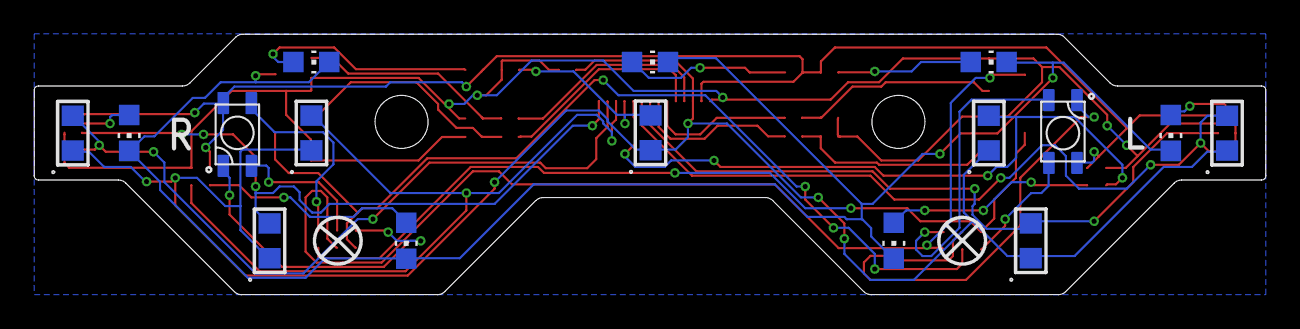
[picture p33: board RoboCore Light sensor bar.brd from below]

Board: 2 copper layers, 72.0 x 15.2 mm, 50 parts (16 on the bottom side), 35 nets.

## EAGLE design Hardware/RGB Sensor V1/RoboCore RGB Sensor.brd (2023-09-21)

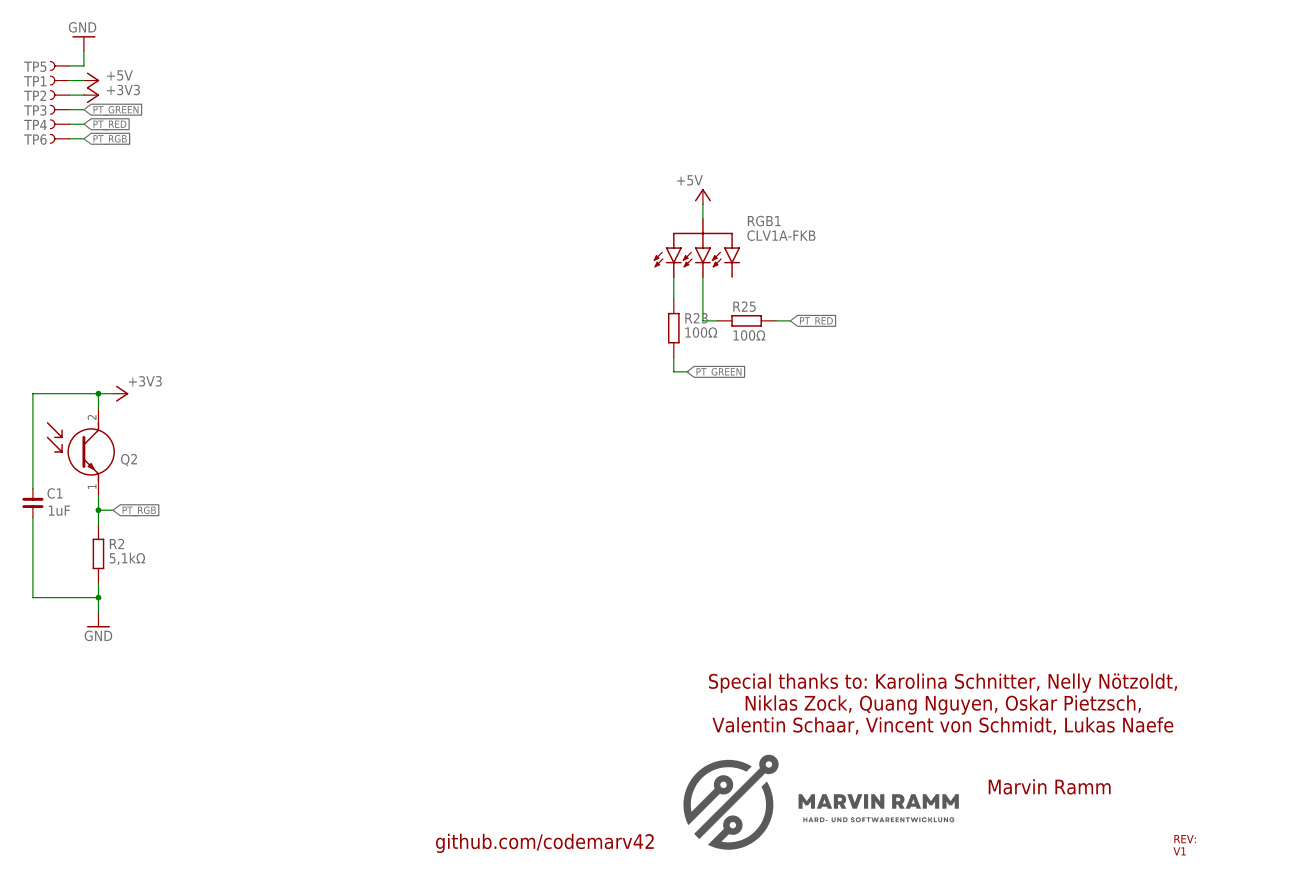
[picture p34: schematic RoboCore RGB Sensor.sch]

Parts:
C1: 1uF; C0402
Q2: PT17-21C/L41/TR8; 0805
R2: 5,1kΩ; R0402
R23, R25: 100Ω; R0402
RGB1: RGBLED
TP1, TP2, TP3, TP4, TP5, TP6: TEST-POINT3X5; PAD.03X.05

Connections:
+3V3: C1.2, Q2.2 (C), TP2.1
+5V: RGB1.+5V, TP1.1
GND: C1.1, R2.2, TP5.1
unnamed: R23.1, RGB1.P3
unnamed: R25.1, RGB1.P2
PT_GREEN: R23.2, TP3.1
PT_RED: R25.2, TP4.1
PT_RGB: Q2.1 (E), R2.1, TP6.1

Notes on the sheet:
RGB1
CLV1A-FKB
Marvin Ramm
REV: V1
github.com/codemarv42
Special thanks to: Karolina Schnitter, Nelly Nötzoldt, Niklas Zock, Quang Nguyen, Oskar Pietzsch, Valentin Schaar, Vincent von Schmidt, Lukas Naefe

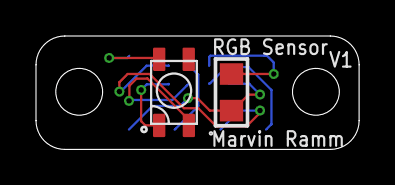
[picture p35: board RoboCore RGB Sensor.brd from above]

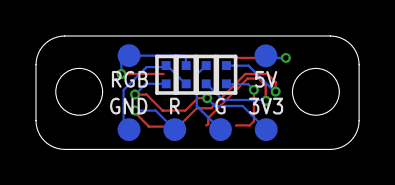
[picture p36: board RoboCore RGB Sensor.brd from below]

Board: 2 copper layers, 17.9 x 6.3 mm, 12 parts (10 on the bottom side), 8 nets.

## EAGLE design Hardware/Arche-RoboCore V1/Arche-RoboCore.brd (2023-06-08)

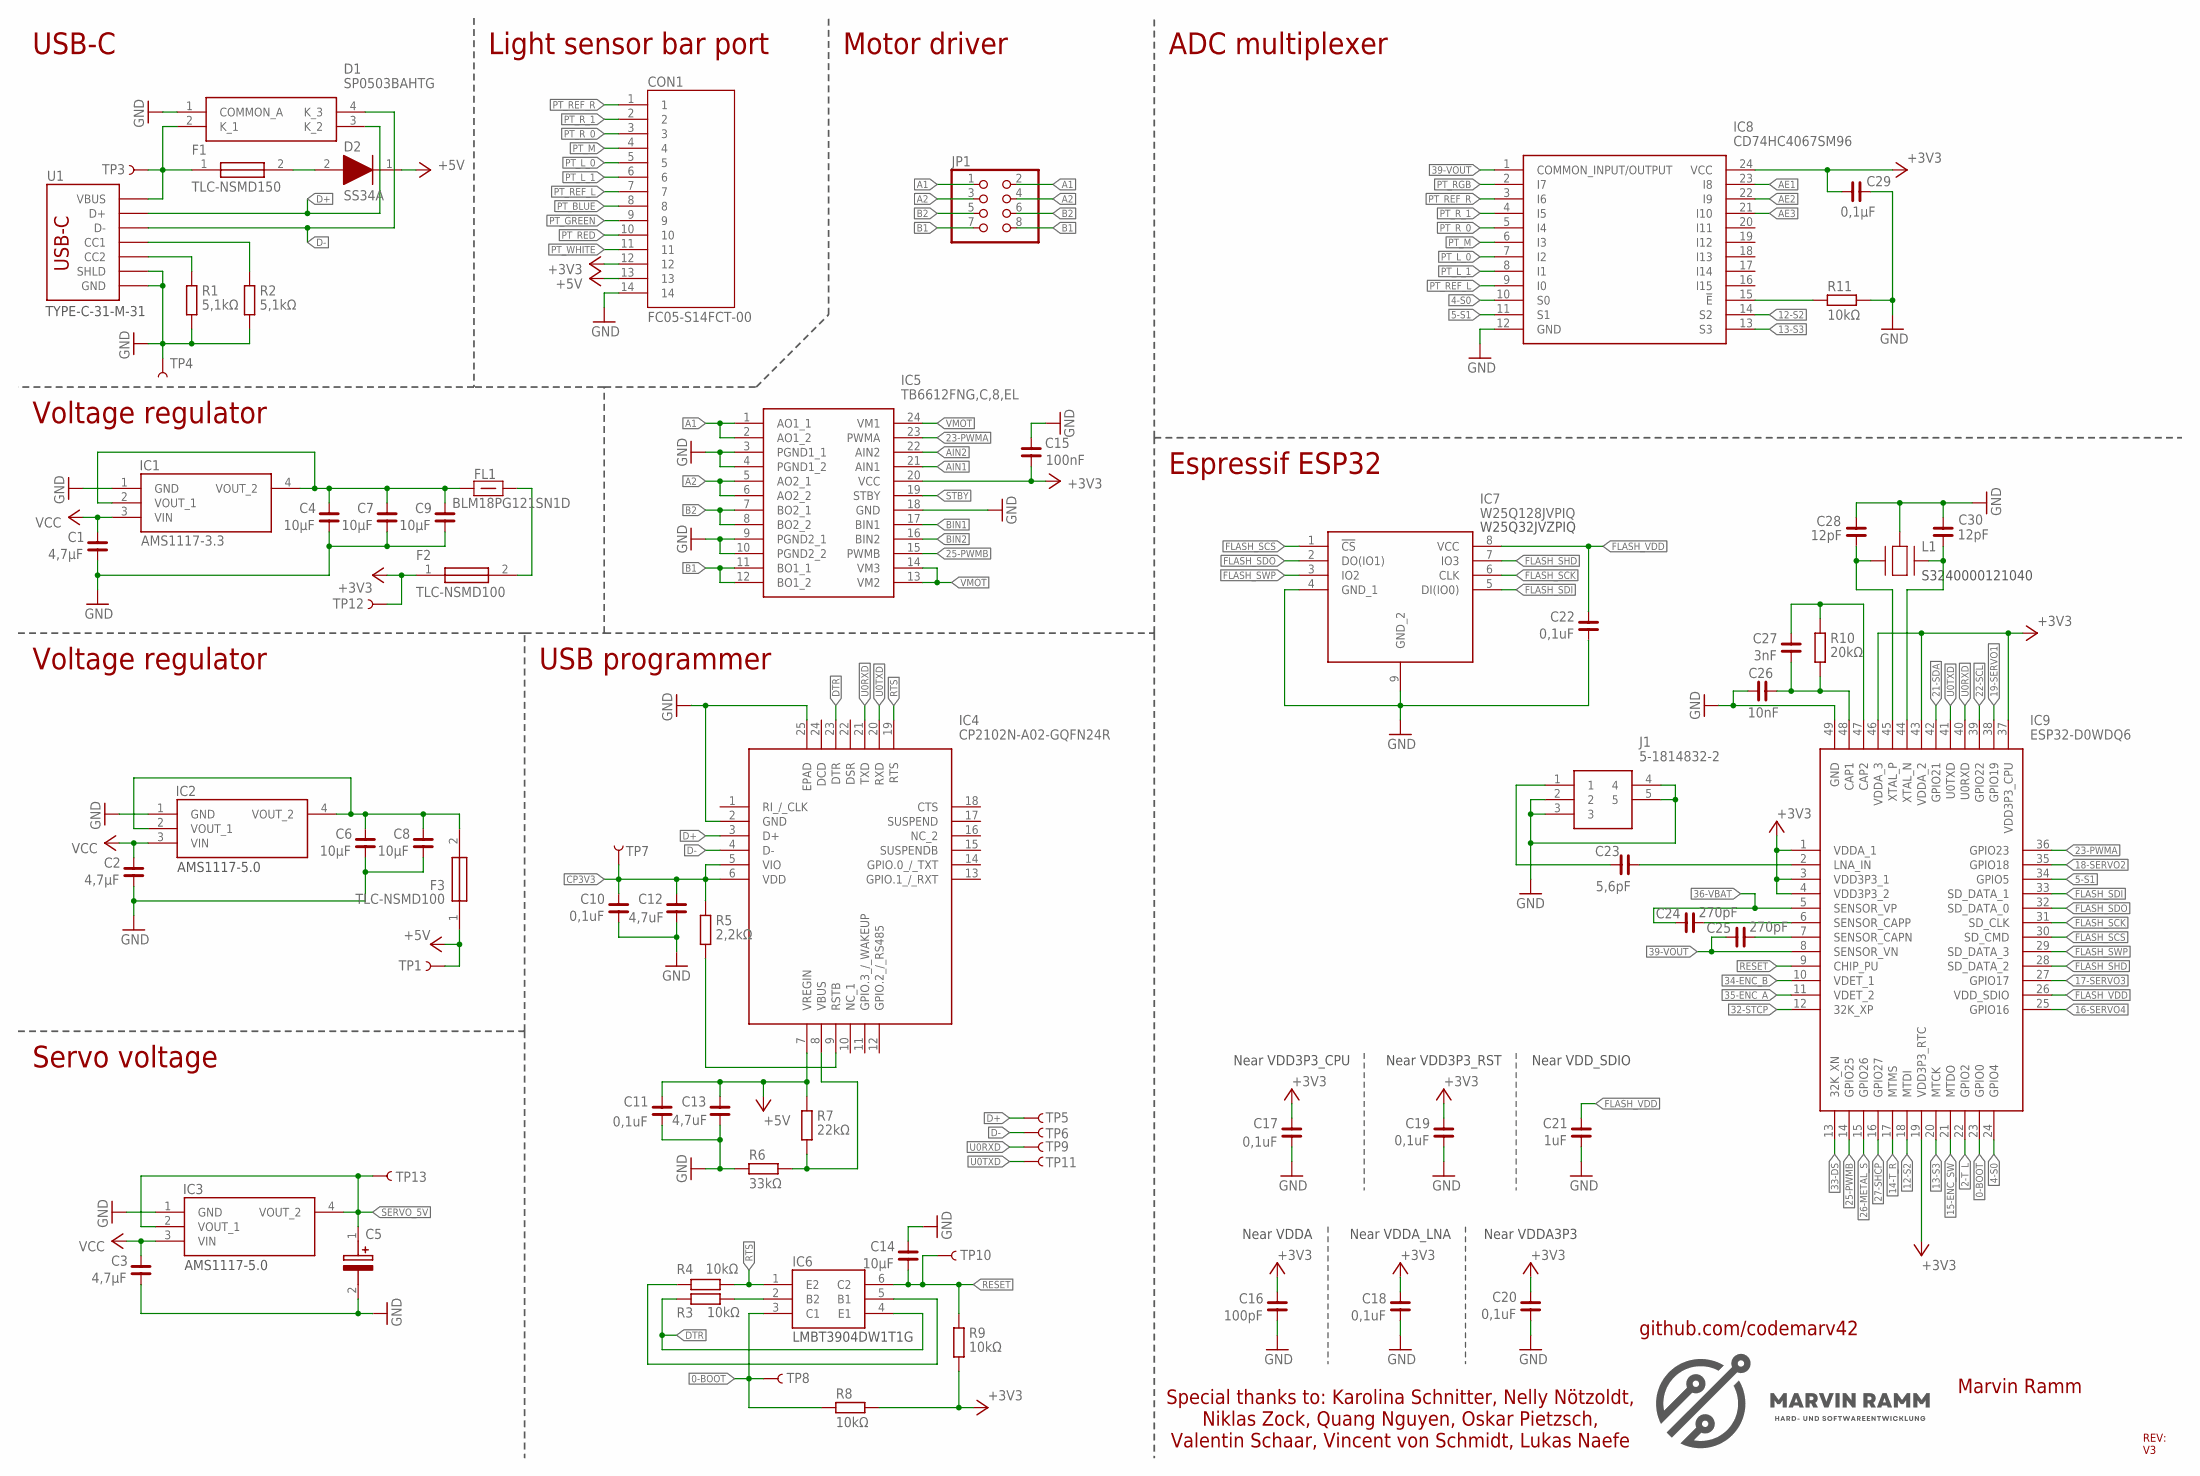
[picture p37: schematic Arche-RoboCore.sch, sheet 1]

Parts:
C1, C2, C3: 4,7µF; C0603
C4, C6, C7, C8, C9, C14: 10µF; C0603
C5: UUD1C151MCL1GS; CAPAE660X800N
C10, C11, C17, C18, C19, C20, C22: 0,1uF; C0402
C12, C13: 4,7uF; C0402
C15: 100nF; C0402
C16: 100pF; C0402
C21: 1uF; C0402
C23: 5,6pF; C0402
C24, C25: 270pF; C0402
C26: 10nF; C0402
C27: 3nF; C0402
C28, C30: 12pF; C0402
C29: 0,1µF; C0402
CON1: FC05-S14FCT-00
D1: SP0503BAHTG
D2: SS34A; DIOM5026X262N
F1, F2, F3: NANOSMDC020F-2; FUSC3216X82N
FL1: BLM18PG121SN1D; BLM18AG102BH1D
IC1, IC2, IC3: AMS1117-3.3; SOT229P700X180-4N
IC4: CP2102N-A02-GQFN24R; QFN50P400X400X80-25N
IC5: TB6612FNG,C,8,EL; SOP65P760X160-24N
IC6: MMDT3904-TP; SOT65P230X120-6N
IC7: W25Q128JVPIQ; SON127P800X600X80-9N
IC8: CD74HC4067SM96; SOP65P780X200-24N
IC9: ESP32-D0WDQ6; QFN40P600X600X90-49N
J1: 5-1814832-2; 518148322
JP1: PINHD-2X4; 2X04
L1: SMD-3225_4P16MHZ_20PF_10PPM_-4; SMD3225_4P16MHZ20PF10PPM4085
R1, R2: 5,1kΩ; R0402
R3, R4, R8, R9, R11: 10kΩ; R0402
R5: 2,2kΩ; R0402
R6: 33kΩ; R0402
R7: 22kΩ; R0402
R10: 20kΩ; R0402
TP1, TP3, TP4, TP5, TP6, TP7, TP8, TP9, TP10, TP11, TP12, TP13: TEST-POINT3X5; PAD.03X.05
U1: TYPE-C-31-M-14; TYPE-C-31-M-14_HRO

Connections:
0-BOOT: IC6.3 (C1), IC9.23 (GPIO0), R8.2, TP8.1
2-T_L: IC9.22 (GPIO2); also elsewhere on the board
4-S0: IC8.10 (S0), IC9.24 (GPIO4)
5-S1: IC8.11 (S1), IC9.34 (GPIO5)
12-S2: IC8.14 (S2), IC9.18 (MTDI)
13-S3: IC8.13 (S3), IC9.20 (MTCK)
14-T_R: IC9.17 (MTMS); also elsewhere on the board
15-ENC_SW: IC9.21 (MTDO); also elsewhere on the board
16-SERVO4: IC9.25 (GPIO16); also elsewhere on the board
17-SERVO3: IC9.27 (GPIO17); also elsewhere on the board
18-SERVO2: IC9.35 (GPIO18); also elsewhere on the board
19-SERVO1: IC9.38 (GPIO19); also elsewhere on the board
21-SDA: IC9.42 (GPIO21); also elsewhere on the board
22-SCL: IC9.39 (GPIO22); also elsewhere on the board
23-PWMA: IC5.23 (PWMA), IC9.36 (GPIO23)
25-PWMB: IC5.15 (PWMB), IC9.14 (GPIO25)
26-METAL_S: IC9.15 (GPIO26); also elsewhere on the board
27-SHCP: IC9.16 (GPIO27); also elsewhere on the board
32-STCP: IC9.12 (32K_XP); also elsewhere on the board
33-DS: IC9.13 (32K_XN); also elsewhere on the board
34-ENC_B: IC9.10 (VDET_1); also elsewhere on the board
35-ENC_A: IC9.11 (VDET_2); also elsewhere on the board
36-VBAT: C24.1, IC9.5 (SENSOR_VP); also elsewhere on the board
39-VOUT: C25.1, IC8.1 (COMMON_INPUT/OUTPUT), IC9.8 (SENSOR_VN)
+3V3: C15.1, C16.2, C17.2, C18.2, C19.2, C20.2, C29.1, CON1.12, F2.1, IC5.20 (VCC), IC8.24 (VCC), IC9.1 (VDDA_1), IC9.3 (VDD3P3_1), IC9.4 (VDD3P3_2), IC9.19 (VDD3P3_RTC), IC9.37 (VDD3P3_CPU), IC9.43 (VDDA_2), IC9.46 (VDDA_3), R8.1, R9.2, TP12.1; also elsewhere on the board
+5V: C11.2, C13.2, CON1.13, D2.1 (K), F3.1, IC4.7 (VREGIN), R7.1, TP1.1; also elsewhere on the board
A1: IC5.1 (AO1_1), IC5.2 (AO1_2), JP1.1, JP1.2
A2: IC5.5 (AO2_1), IC5.6 (AO2_2), JP1.3, JP1.4
AE1: IC8.23 (I8); also elsewhere on the board
AE2: IC8.22 (I9); also elsewhere on the board
AE3: IC8.21 (I10); also elsewhere on the board
AIN1: IC5.21 (AIN1); also elsewhere on the board
AIN2: IC5.22 (AIN2); also elsewhere on the board
B1: IC5.11 (BO1_1), IC5.12 (BO1_2), JP1.7, JP1.8
B2: IC5.7 (BO2_1), IC5.8 (BO2_2), JP1.5, JP1.6
BIN1: IC5.17 (BIN1); also elsewhere on the board
BIN2: IC5.16 (BIN2); also elsewhere on the board
CP3V3: C10.2, C12.2, IC4.5 (VIO), IC4.6 (VDD), R5.1, TP7.1
D+: D1.3 (K_2), IC4.3 (D+), TP5.1, U1.A6 (D+), U1.B6 (D+)
D-: D1.4 (K_3), IC4.4 (D-), TP6.1, U1.A7 (D-), U1.B7 (D-)
DTR: IC4.23 (DTR), IC6.4 (E1), R3.2
FLASH_SCK: IC7.6 (CLK), IC9.31 (SD_CLK)
FLASH_SCS: IC7.1 (!CS), IC9.30 (SD_CMD)
FLASH_SDI: IC7.5 (DI(IO0)), IC9.33 (SD_DATA_1)
FLASH_SDO: IC7.2 (DO(IO1)), IC9.32 (SD_DATA_0)
FLASH_SHD: IC7.7 (IO3), IC9.28 (SD_DATA_2)
FLASH_SWP: IC7.3 (IO2), IC9.29 (SD_DATA_3)
FLASH_VDD: C21.2, C22.2, IC7.8 (VCC), IC9.26 (VDD_SDIO)
GND: C1.2, C2.2, C3.2, C4.2, C5.2 (-), C6.2, C7.2, C8.2, C9.2, C10.1, C11.1, C12.1, C13.1, C14.1, C15.2, C16.1, C17.1, C18.1, C19.1, C20.1, C21.1, C22.1, C26.1, C28.1, C29.2, C30.1, CON1.14, D1.1 (COMMON_A), IC1.1 (GND), IC2.1 (GND), IC3.1 (GND), IC4.2 (GND), IC4.25 (EPAD), IC5.3 (PGND1_1), IC5.4 (PGND1_2), IC5.9 (PGND2_1), IC5.10 (PGND2_2), IC5.18 (GND), IC7.4 (GND_1), IC7.9 (GND_2), IC8.12 (GND), IC9.49 (GND), J1.2, J1.3, J1.4, J1.5, L1.2 (GND_2), L1.4 (GND_2), R1.2, R2.2, R6.2, R11.2, TP4.1, U1.A1B12 (GND), U1.B1A12 (GND), U1.P$1 (SHLD), U1.P$2 (SHLD), U1.P$3 (SHLD), U1.P$4 (SHLD), U1.P$5 (SHLD), U1.P$6 (SHLD), U1.P$7 (SHLD), U1.P$8 (SHLD), U1.P$9 (SHLD), U1.P$10 (SHLD), U1.P$11 (SHLD), U1.P$12 (SHLD), U1.P$14 (SHLD), U1.P$16 (SHLD), U1.P$18 (SHLD), U1.P$20 (SHLD); also elsewhere on the board
unnamed: D2.2 (A), F1.2
unnamed: C6.1, C8.1, F3.2, IC2.2 (VOUT_1), IC2.4 (VOUT_2)
unnamed: F2.2, FL1.1
unnamed: C4.1, C7.1, C9.1, FL1.2, IC1.2 (VOUT_1), IC1.4 (VOUT_2)
unnamed: R1.1, U1.B5 (CC2)
unnamed: R2.1, U1.A5 (CC1)
unnamed: IC4.9 (RSTB), R5.2
unnamed: IC4.8 (VBUS), R6.1, R7.2
unnamed: IC8.15 (!E), R11.1
unnamed: C23.1, IC9.2 (LNA_IN)
unnamed: C26.2, C27.1, IC9.48 (CAP1), R10.2
unnamed: C27.2, IC9.47 (CAP2), R10.1
unnamed: C30.2, IC9.44 (XTAL_N), L1.3 (CRYSTAL_2)
unnamed: C28.2, IC9.45 (XTAL_P), L1.1 (CRYSTAL_1)
unnamed: C23.2, J1.1
unnamed: IC6.5 (B1), R4.2
unnamed: IC6.2 (B2), R3.1
unnamed: C25.2, IC9.7 (SENSOR_CAPN)
unnamed: C24.2, IC9.6 (SENSOR_CAPP)
PT_BLUE: CON1.8; also elsewhere on the board
PT_GREEN: CON1.9; also elsewhere on the board
PT_L_0: CON1.5, IC8.7 (I2)
PT_L_1: CON1.6, IC8.8 (I1)
PT_M: CON1.4, IC8.6 (I3)
PT_RED: CON1.10; also elsewhere on the board
PT_REF_L: CON1.7, IC8.9 (I0)
PT_REF_R: CON1.1, IC8.3 (I6)
PT_RGB: IC8.2 (I7); also elsewhere on the board
PT_R_0: CON1.3, IC8.5 (I4)
PT_R_1: CON1.2, IC8.4 (I5)
PT_WHITE: CON1.11; also elsewhere on the board
RESET: C14.2, IC6.6 (C2), IC9.9 (CHIP_PU), R9.1, TP10.1
RTS: IC4.19 (RTS), IC6.1 (E2), R4.1
SERVO_5V: C5.1 (+), IC3.2 (VOUT_1), IC3.4 (VOUT_2), TP13.1; also elsewhere on the board
STBY: IC5.19 (STBY); also elsewhere on the board
U0RXD: IC4.21 (TXD), IC9.40 (U0RXD), TP9.1
U0TXD: IC4.20 (RXD), IC9.41 (U0TXD), TP11.1
USBDIRECT: D1.2 (K_1), F1.1, TP3.1, U1.A4B9 (VBUS), U1.B4A9 (VBUS)
VCC: C1.1, C2.1, C3.1, IC1.3 (VIN), IC2.3 (VIN), IC3.3 (VIN); also elsewhere on the board
VMOT: IC5.13 (VM2), IC5.14 (VM3), IC5.24 (VM1); also elsewhere on the board

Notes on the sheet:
AMS1117-5.0
S3240000121040
Near VDDA
Near VDDA_LNA
Near VDDA3P3
Near VDD3P3_CPU
Near VDD3P3_RST
Near VDD_SDIO
W25Q32JVZPIQ
TYPE-C-31-M-31
TLC-NSMD150
LMBT3904DW1T1G
Marvin Ramm
REV: V3
USB-C
ADC multiplexer
Espressif ESP32
Voltage regulator
USB programmer
github.com/codemarv42
TLC-NSMD100
Motor driver
Light sensor bar port
Servo voltage
Special thanks to: Karolina Schnitter, Nelly Nötzoldt, Niklas Zock, Quang Nguyen, Oskar Pietzsch, Valentin Schaar, Vincent von Schmidt, Lukas Naefe

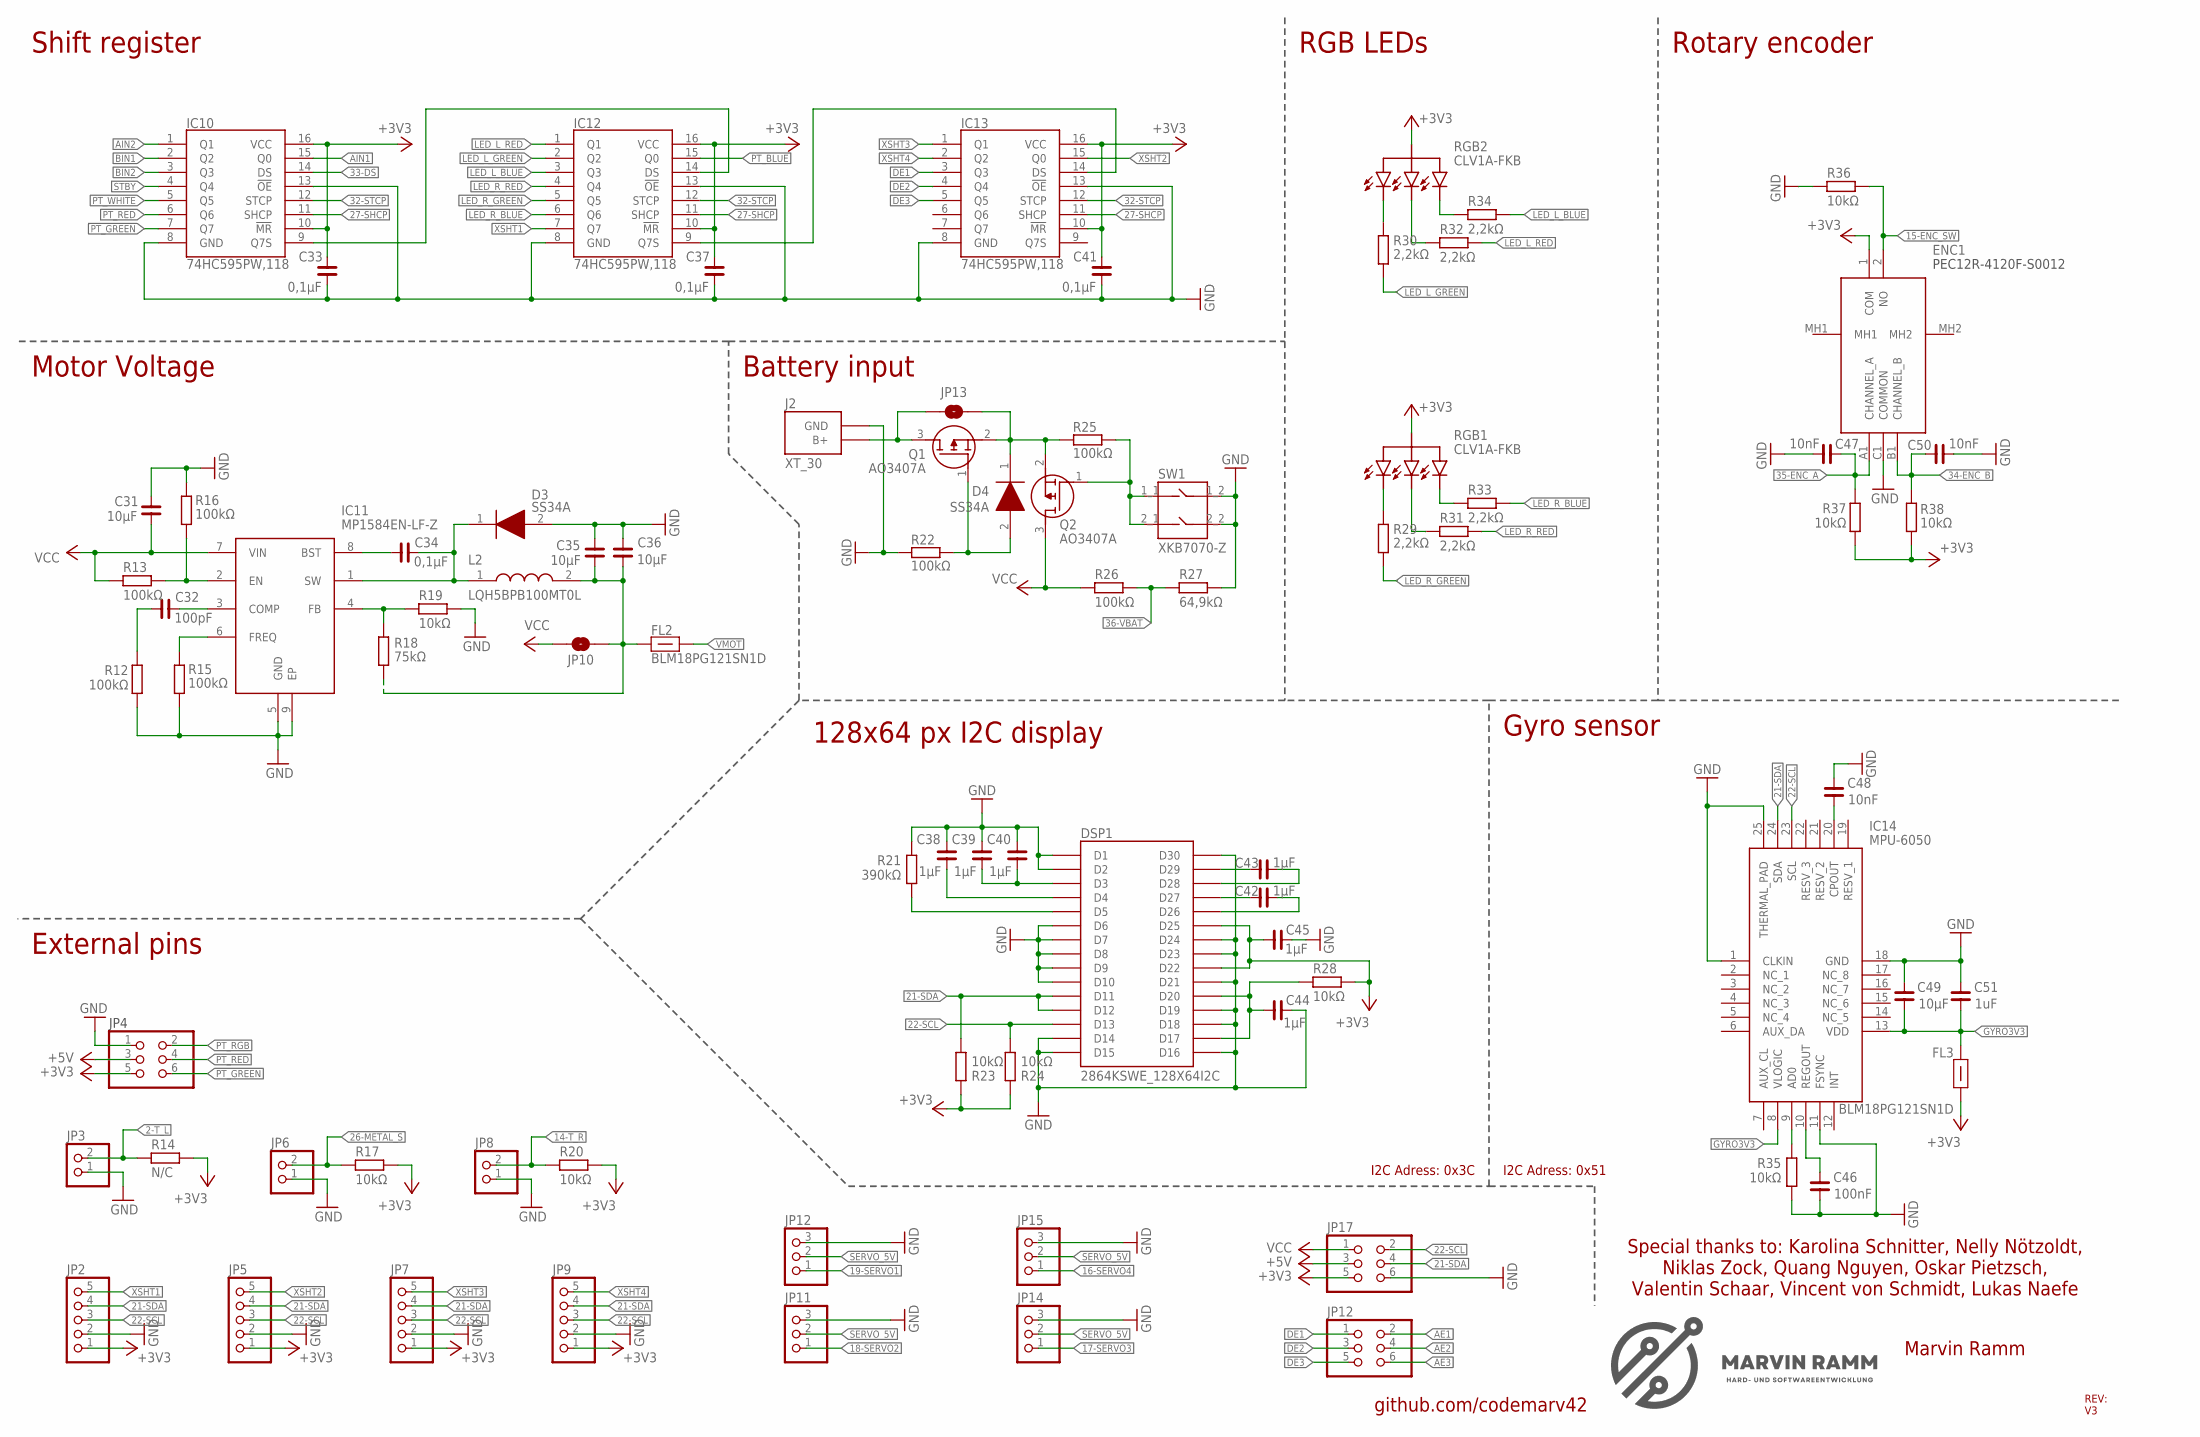
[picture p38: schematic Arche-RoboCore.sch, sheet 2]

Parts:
C31, C35, C36, C49: 10µF; C0603
C32: 100pF; C0402
C33, C34, C37, C41: 0,1µF; C0402
C38, C39, C40, C42, C43, C44, C45: 1µF; C0402
C46: 100nF; C0402
C47, C48, C50: 10nF; C0402
C51: 1uF; C0402
D3, D4: SS34A; DIOM5026X262N
DSP1: 2864KSWE_128X64I2C
ENC1: PEC12R-4230F-S0024; PEC12R4230FS0024
FL2, FL3: BLM18PG121SN1D; BLM18AG102BH1D
IC10, IC12, IC13: 74HC595PW,118; SOP65P640X110-16N
IC11: MP1584EN-LF-Z; SOIC127P600X170-9N
IC14: MPU-6050; QFN50P400X400X95-25N
J2: XT_30
JP2, JP5, JP7, JP9: PINHD-1X5; 1X05
JP3, JP6, JP8: PINHD-1X2; 1X02
JP4, JP16, JP17: PINHD-2X3; 2X03
JP10, JP13: JUMPER-SMT_2_NO_SILK; SMT-JUMPER_2_NO_SILK
JP11, JP12, JP14, JP15: PINHD-1X3; 1X03
L2: LQH5BPB100MT0L
Q1, Q2: AO3407A; SOT95P280X125-3N
R12, R13, R15, R16, R22, R25, R26: 100kΩ; R0402
R14: N/C; R0402
R17, R19, R20, R23, R24, R28, R35, R36, R37, R38: 10kΩ; R0402
R18: 75kΩ; R0402
R21: 390kΩ; R0402
R27: 64,9kΩ; R0402
R29, R30, R31, R32, R33, R34: 2,2kΩ; R0402
RGB1, RGB2: RGBLED
SW1: XKB7070-Z

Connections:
2-T_L: JP3.2, R14.1; also elsewhere on the board
14-T_R: JP8.2, R20.1; also elsewhere on the board
15-ENC_SW: ENC1.2 (NO), R36.2; also elsewhere on the board
16-SERVO4: JP15.1; also elsewhere on the board
17-SERVO3: JP14.1; also elsewhere on the board
18-SERVO2: JP11.1; also elsewhere on the board
19-SERVO1: JP12.1; also elsewhere on the board
21-SDA: DSP1.D11, DSP1.D12, IC14.24 (SDA), JP2.4, JP5.4, JP7.4, JP9.4, JP17.4, R23.1; also elsewhere on the board
22-SCL: DSP1.D13, IC14.23 (SCL), JP2.3, JP5.3, JP7.3, JP9.3, JP17.2, R24.1; also elsewhere on the board
26-METAL_S: JP6.2, R17.1; also elsewhere on the board
27-SHCP: IC10.11 (SHCP), IC12.11 (SHCP), IC13.11 (SHCP); also elsewhere on the board
32-STCP: IC10.12 (STCP), IC12.12 (STCP), IC13.12 (STCP); also elsewhere on the board
33-DS: IC10.14 (DS); also elsewhere on the board
34-ENC_B: C50.1, ENC1.B1 (CHANNEL_B), R38.2; also elsewhere on the board
35-ENC_A: C47.1, ENC1.A1 (CHANNEL_A), R37.2; also elsewhere on the board
36-VBAT: R26.2, R27.1; also elsewhere on the board
+3V3: C33.1, C37.1, C41.1, C45.1, DSP1.D22, DSP1.D25, ENC1.1 (COM), FL3.1, IC10.10 (!MR), IC10.16 (VCC), IC12.10 (!MR), IC12.16 (VCC), IC13.10 (!MR), IC13.16 (VCC), JP2.1, JP4.5, JP5.1, JP7.1, JP9.1, JP17.5, R14.2, R17.2, R20.2, R23.2, R24.2, R28.2, R37.1, R38.1, RGB1.+5V, RGB2.+5V; also elsewhere on the board
+5V: JP4.3, JP17.3; also elsewhere on the board
AE1: JP16.2; also elsewhere on the board
AE2: JP16.4; also elsewhere on the board
AE3: JP16.6; also elsewhere on the board
AIN1: IC10.15 (Q0); also elsewhere on the board
AIN2: IC10.1 (Q1); also elsewhere on the board
BIN1: IC10.2 (Q2); also elsewhere on the board
BIN2: IC10.3 (Q3); also elsewhere on the board
DE1: IC13.3 (Q3), JP16.1
DE2: IC13.4 (Q4), JP16.3
DE3: IC13.5 (Q5), JP16.5
GND: C31.1, C33.2, C35.1, C36.1, C37.2, C38.1, C39.1, C40.1, C41.2, C44.2, C45.2, C46.1, C47.2, C48.2, C49.1, C50.2, C51.2, D3.2 (A), DSP1.D1, DSP1.D2, DSP1.D6, DSP1.D7, DSP1.D8, DSP1.D9, DSP1.D10, DSP1.D14, DSP1.D15, DSP1.D16, DSP1.D18, DSP1.D19, DSP1.D21, DSP1.D23, DSP1.D24, DSP1.D30, ENC1.C1 (COMMON), IC10.8 (GND), IC10.13 (!OE), IC11.5 (GND), IC11.9 (EP), IC12.8 (GND), IC12.13 (!OE), IC13.8 (GND), IC13.13 (!OE), IC14.1 (CLKIN), IC14.11 (FSYNC), IC14.18 (GND), IC14.25 (THERMAL_PAD), J2.GND, JP2.2, JP3.1, JP4.1, JP5.2, JP6.1, JP7.2, JP8.1, JP9.2, JP11.3, JP12.3, JP14.3, JP15.3, JP17.6, R12.2, R15.2, R16.1, R19.1, R21.2, R22.1, R27.2, R35.1, R36.1, SW1.1_2, SW1.2_2; also elsewhere on the board
GYRO3V3: C49.2, C51.1, FL3.2, IC14.8 (VLOGIC), IC14.13 (VDD)
LED_L_BLUE: IC12.3 (Q3), R34.2
LED_L_GREEN: IC12.2 (Q2), R30.2
LED_L_RED: IC12.1 (Q1), R32.2
LED_R_BLUE: IC12.6 (Q6), R33.2
LED_R_GREEN: IC12.5 (Q5), R29.2
LED_R_RED: IC12.4 (Q4), R31.2
unnamed: C48.1, IC14.20 (CPOUT)
unnamed: C46.2, IC14.10 (REGOUT)
unnamed: IC14.9 (AD0), R35.2
unnamed: Q2.1 (G), R25.2, SW1.1_1, SW1.2_1
unnamed: IC12.9 (Q7S), IC13.14 (DS)
unnamed: D4.1 (K), JP13.1, Q1.2 (S), Q2.2 (S), R25.1
unnamed: D4.2 (A), Q1.1 (G), R22.2
unnamed: J2.B+, JP13.2, Q1.3 (D)
unnamed: C35.2, C36.2, FL2.2, JP10.1, L2.2, R18.2
unnamed: IC11.2 (EN), R13.1, R16.2
unnamed: IC11.6 (FREQ), R15.1
unnamed: C32.2, IC11.3 (COMP)
unnamed: C42.1, DSP1.D27
unnamed: C44.1, DSP1.D17, DSP1.D20, R28.1
unnamed: C38.2, DSP1.D4
unnamed: C42.2, DSP1.D26
unnamed: C39.2, C40.2, DSP1.D3
unnamed: DSP1.D5, R21.1
unnamed: C43.1, DSP1.D29
unnamed: C43.2, DSP1.D28
unnamed: C32.1, R12.1
unnamed: C34.2, D3.1 (K), IC11.1 (SW), L2.1
unnamed: R30.1, RGB2.P3
unnamed: R34.1, RGB2.P1
unnamed: R32.1, RGB2.P2
unnamed: C34.1, IC11.8 (BST)
unnamed: IC10.9 (Q7S), IC12.14 (DS)
unnamed: R29.1, RGB1.P3
unnamed: R33.1, RGB1.P1
unnamed: R31.1, RGB1.P2
unnamed: IC11.4 (FB), R18.1, R19.2
PT_BLUE: IC12.15 (Q0); also elsewhere on the board
PT_GREEN: IC10.7 (Q7), JP4.6; also elsewhere on the board
PT_RED: IC10.6 (Q6), JP4.4; also elsewhere on the board
PT_RGB: JP4.2; also elsewhere on the board
PT_WHITE: IC10.5 (Q5); also elsewhere on the board
SERVO_5V: JP11.2, JP12.2, JP14.2, JP15.2; also elsewhere on the board
STBY: IC10.4 (Q4); also elsewhere on the board
VCC: C31.2, IC11.7 (VIN), JP10.2, JP17.1, Q2.3 (D), R13.2, R26.1; also elsewhere on the board
VMOT: FL2.1; also elsewhere on the board
XSHT1: IC12.7 (Q7), JP2.5
XSHT2: IC13.15 (Q0), JP5.5
XSHT3: IC13.1 (Q1), JP7.5
XSHT4: IC13.2 (Q2), JP9.5

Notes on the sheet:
RGB2
CLV1A-FKB
Marvin Ramm
REV: V3
Gyro sensor
Rotary encoder
External pins
128x64 px I2C display
I2C Adress: 0x51
PEC12R-4120F-S0012
RGB1
RGB LEDs
github.com/codemarv42
JP12
I2C Adress: 0x3C
Motor Voltage
Shift register
Battery input
JP4
Special thanks to: Karolina Schnitter, Nelly Nötzoldt, Niklas Zock, Quang Nguyen, Oskar Pietzsch, Valentin Schaar, Vincent von Schmidt, Lukas Naefe

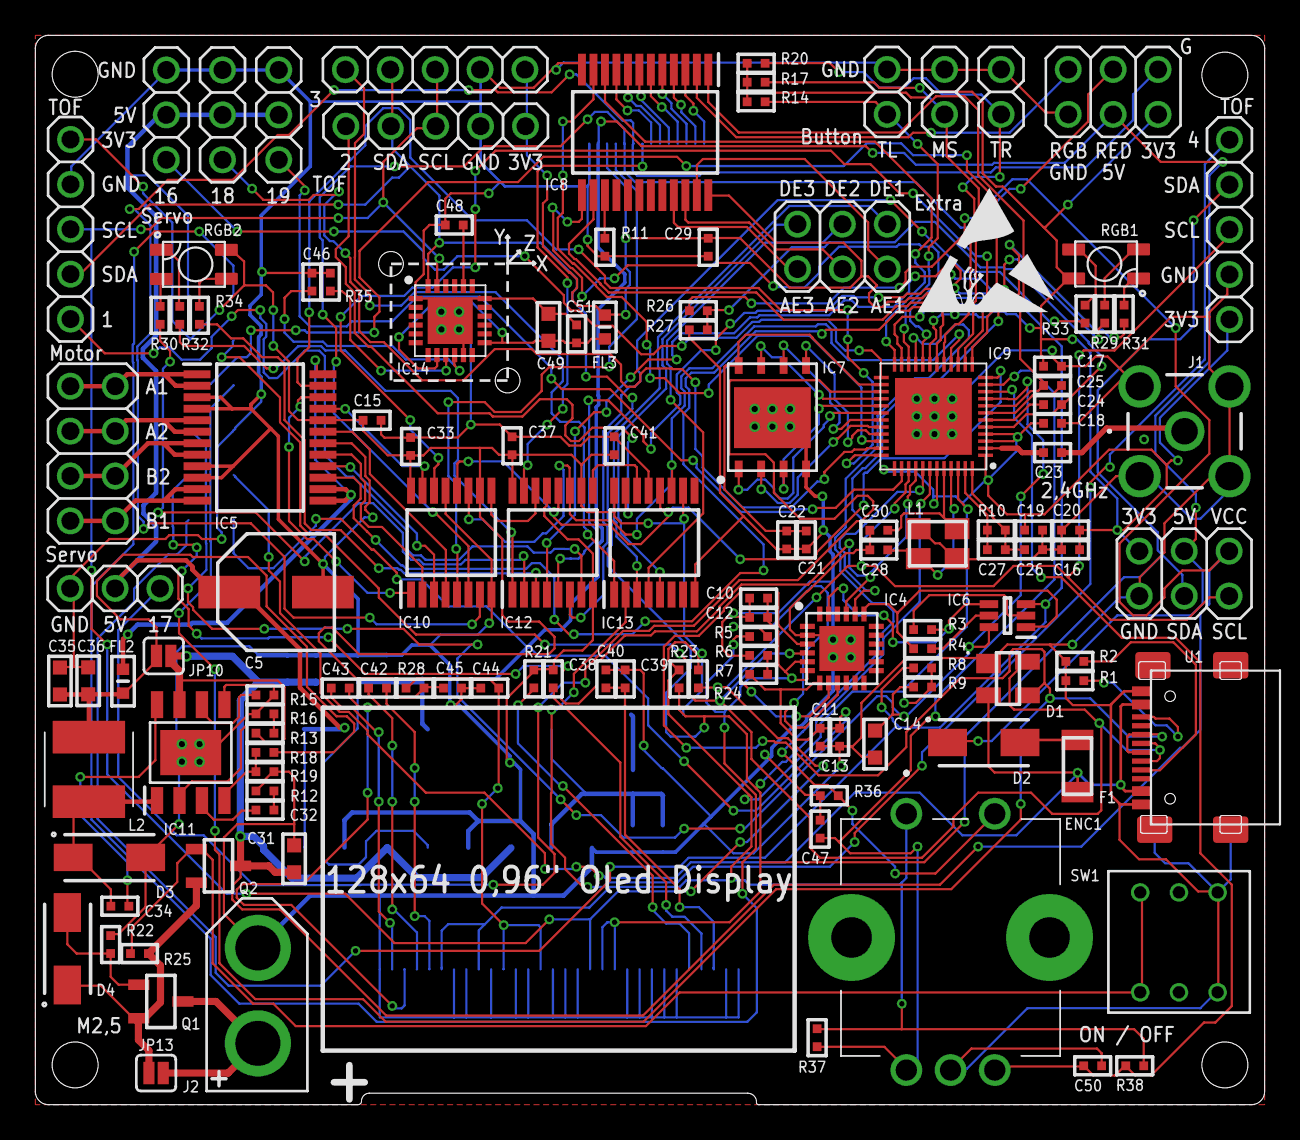
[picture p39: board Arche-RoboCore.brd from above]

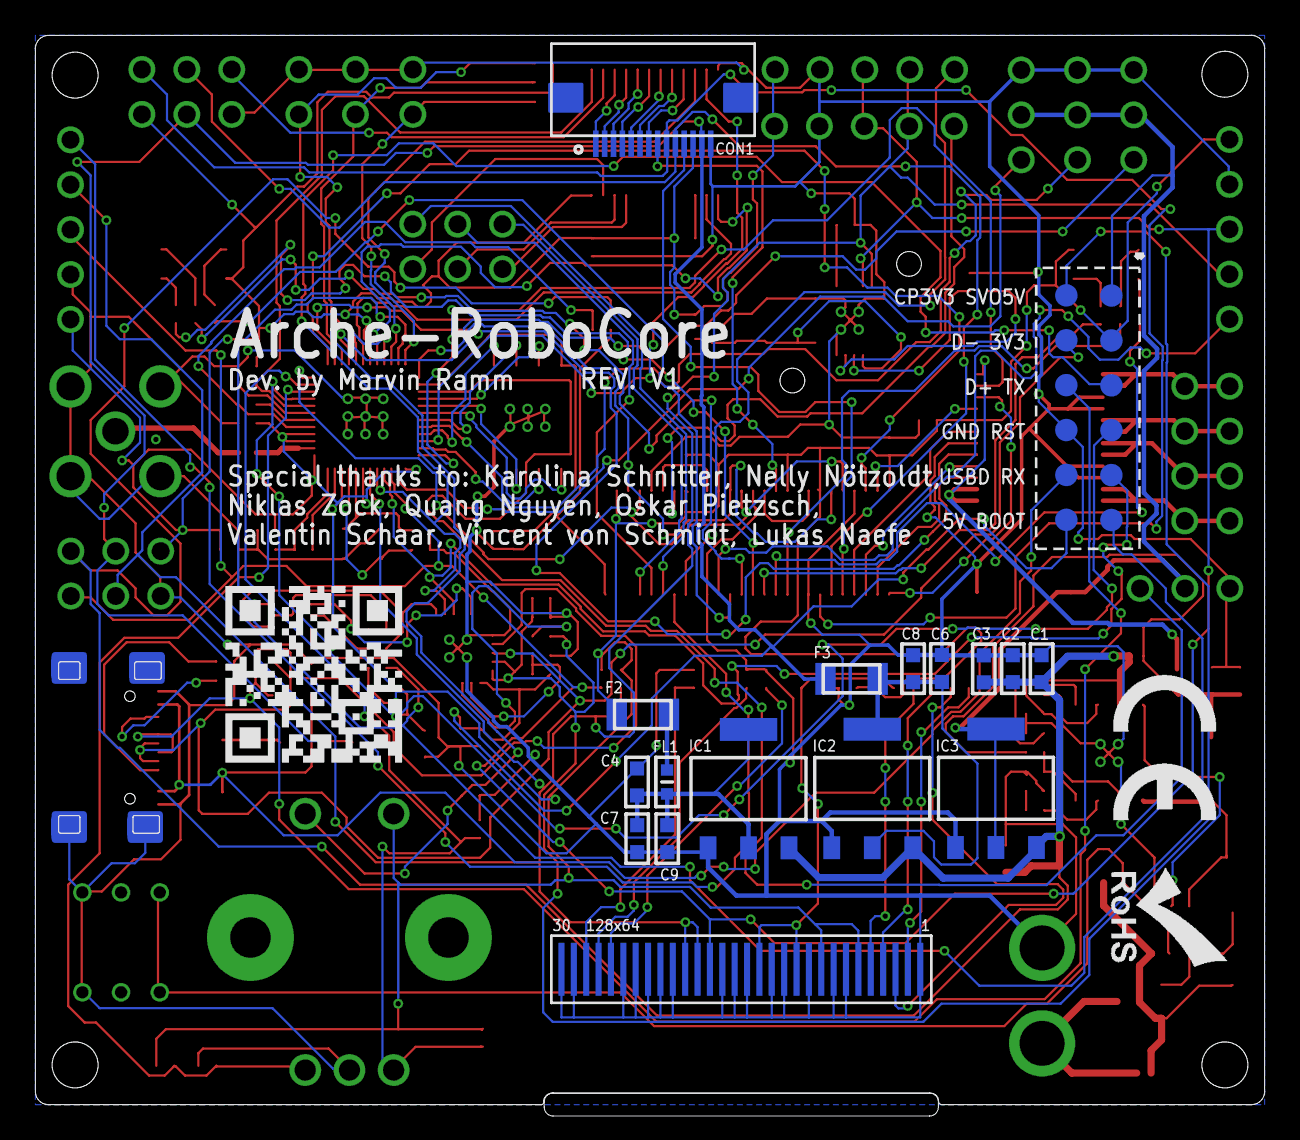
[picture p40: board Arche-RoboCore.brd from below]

Board: 2 copper layers, 69.5 x 60.5 mm, 155 parts (28 on the bottom side), 134 nets.

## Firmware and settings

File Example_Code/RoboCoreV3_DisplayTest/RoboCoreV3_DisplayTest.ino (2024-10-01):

#include "Pins.h"
#include "Bitmap.h"

#include <SPI.h>
#include <Wire.h>
#include <Adafruit_GFX.h> //https://github.com/adafruit/Adafruit-GFX-Library
#include <Adafruit_SSD1306.h> //https://github.com/adafruit/Adafruit_SSD1306

#define SCREEN_WIDTH 128 // OLED display width, in pixels
#define SCREEN_HEIGHT 64 // OLED display height, in pixels

#define OLED_RESET     -1 // Reset pin # (or -1 if sharing Arduino reset pin)
Adafruit_SSD1306 display(SCREEN_WIDTH, SCREEN_HEIGHT, &Wire, OLED_RESET);

#define NUMFLAKES     10 // Number of snowflakes in the animation example

#define LOGO_HEIGHT   16
#define LOGO_WIDTH    16

static const unsigned char PROGMEM logo_bmp[] =
{ 0b00000000, 0b11000000,
  0b00000001, 0b11000000,
  0b00000001, 0b11000000,
  0b00000011, 0b11100000,
  0b11110011, 0b11100000,
  0b11111110, 0b11111000,
  0b01111110, 0b11111111,
  0b00110011, 0b10011111,
  0b00011111, 0b11111100,
  0b00001101, 0b01110000,
  0b00011011, 0b10100000,
  0b00111111, 0b11100000,
  0b00111111, 0b11110000,
  0b01111100, 0b11110000,
  0b01110000, 0b01110000,
  0b00000000, 0b00110000 };

void setup() {
  Serial.begin(115200);

  // SSD1306_SWITCHCAPVCC = generate display voltage from 3.3V internally
  if(!display.begin(SSD1306_SWITCHCAPVCC, OLED_ADRESS)) {
    Serial.println(F("SSD1306 allocation failed"));
    for(;;); // Don't proceed, loop forever
  }

  // Show initial display buffer contents on the screen --
  // the library initializes this with an Adafruit splash screen.
  display.display();
  delay(2000); // Pause for 2 seconds

  // Clear the buffer
  display.clearDisplay();

  // Draw a single pixel in white
  display.drawPixel(10, 10, SSD1306_WHITE);

  // Show the display buffer on the screen. You MUST call display() after
  // drawing commands to make them visible on screen!
  display.display();
  delay(2000);
  // display.display() is NOT necessary after every single drawing command,
  // unless that's what you want...rather, you can batch up a bunch of
  // drawing operations and then update the screen all at once by calling
  // display.display(). These examples demonstrate both approaches...

  testdrawline();      // Draw many lines

  testdrawrect();      // Draw rectangles (outlines)

  testfillrect();      // Draw rectangles (filled)

  testdrawcircle();    // Draw circles (outlines)

  testfillcircle();    // Draw circles (filled)

  testdrawroundrect(); // Draw rounded rectangles (outlines)

  testfillroundrect(); // Draw rounded rectangles (filled)

  testdrawtriangle();  // Draw triangles (outlines)

  testfilltriangle();  // Draw triangles (filled)

  testdrawchar();      // Draw characters of the default font

  //testdrawstyles();    // Draw 'stylized' characters

  //testscrolltext();    // Draw scrolling text

  //testdrawbitmap();    // Draw a small bitmap image

  // Invert and restore display, pausing in-between
  display.invertDisplay(true);
  delay(1000);
  display.invertDisplay(false);
  delay(1000);

  //testanimate(logo_bmp, LOGO_WIDTH, LOGO_HEIGHT); // Animate bitmaps
}

void loop() {
  display.clearDisplay();
  display.drawBitmap(0, 0, FollowLineBitmap, 128, 64, SSD1306_WHITE);
  display.display();

  delay(2000);

  display.clearDisplay();
  display.drawBitmap(0, 0, LeftBlackBitmap, 128, 64, SSD1306_WHITE);
  display.display();

  delay(2000);

  display.clearDisplay();
  display.drawBitmap(0, 0, RightBlackBitmap, 128, 64, SSD1306_WHITE);
  display.display();

  delay(2000);

  display.clearDisplay();
  display.drawBitmap(0, 0, GapBitmap, 128, 64, SSD1306_WHITE);
  display.display();

  delay(2000);

  display.clearDisplay();
  display.drawBitmap(0, 0, LeftGreenBitmap, 128, 64, SSD1306_WHITE);
  display.display();

  delay(2000);

  display.clearDisplay();
  display.drawBitmap(0, 0, RightGreenBitmap, 128, 64, SSD1306_WHITE);
  display.display();

  delay(2000);

  display.clearDisplay();
  display.drawBitmap(0, 0, TurnBitmap, 128, 64, SSD1306_WHITE);
  display.display();

  delay(2000);

  display.clearDisplay();
  display.drawBitmap(0, 0, EndBitmap, 128, 64, SSD1306_WHITE);
  display.display();

  delay(2000);

  display.clearDisplay();
  display.drawBitmap(0, 0, ObstacleBitmap, 128, 64, SSD1306_WHITE);
  display.display();

  delay(2000);

  display.clearDisplay();
  display.drawBitmap(0, 0, FollowLineUpBitmap, 128, 64, SSD1306_WHITE);
  display.display();

  delay(2000);

  display.clearDisplay();
  display.drawBitmap(0, 0, FollowLineDownBitmap, 128, 64, SSD1306_WHITE);
  display.display();

  delay(2000);

  display.clearDisplay();
  display.drawBitmap(0, 0, RescueBitmap, 128, 64, SSD1306_WHITE);
  display.display();

  delay(2000);
  display.clearDisplay();
  display.drawBitmap(0, 0, CrossingBitmap, 128, 64, SSD1306_WHITE);
  display.display();

  delay(2000);
}

void testdrawline() {
  int16_t i;

  display.clearDisplay(); // Clear display buffer

  for(i=0; i<display.width(); i+=4) {
    display.drawLine(0, 0, i, display.height()-1, SSD1306_WHITE);
    display.display(); // Update screen with each newly-drawn line
    delay(1);
  }
  for(i=0; i<display.height(); i+=4) {
    display.drawLine(0, 0, display.width()-1, i, SSD1306_WHITE);
    display.display();
    delay(1);
  }
  delay(250);

  display.clearDisplay();

  for(i=0; i<display.width(); i+=4) {
    display.drawLine(0, display.height()-1, i, 0, SSD1306_WHITE);
    display.display();
    delay(1);
  }
  for(i=display.height()-1; i>=0; i-=4) {
    display.drawLine(0, display.height()-1, display.width()-1, i, SSD1306_WHITE);
    display.display();
    delay(1);
  }
  delay(250);

  display.clearDisplay();

  for(i=display.width()-1; i>=0; i-=4) {
    display.drawLine(display.width()-1, display.height()-1, i, 0, SSD1306_WHITE);
    display.display();
    delay(1);
  }
  for(i=display.height()-1; i>=0; i-=4) {
    display.drawLine(display.width()-1, display.height()-1, 0, i, SSD1306_WHITE);
    display.display();
    delay(1);
  }
  delay(250);

  display.clearDisplay();

  for(i=0; i<display.height(); i+=4) {
    display.drawLine(display.width()-1, 0, 0, i, SSD1306_WHITE);
    display.display();
    delay(1);
  }
  for(i=0; i<display.width(); i+=4) {
    display.drawLine(display.width()-1, 0, i, display.height()-1, SSD1306_WHITE);
    display.display();
    delay(1);
  }

  delay(2000); // Pause for 2 seconds
}

void testdrawrect(void) {
  display.clearDisplay();

  for(int16_t i=0; i<display.height()/2; i+=2) {
    display.drawRect(i, i, display.width()-2*i, display.height()-2*i, SSD1306_WHITE);
    display.display(); // Update screen with each newly-drawn rectangle
    delay(1);
  }

  delay(2000);
}

void testfillrect(void) {
  display.clearDisplay();

  for(int16_t i=0; i<display.height()/2; i+=3) {
    // The INVERSE color is used so rectangles alternate white/black
    display.fillRect(i, i, display.width()-i*2, display.height()-i*2, SSD1306_INVERSE);
    display.display(); // Update screen with each newly-drawn rectangle
    delay(1);
  }

  delay(2000);
}

void testdrawcircle(void) {
  display.clearDisplay();

  for(int16_t i=0; i<max(display.width(),display.height())/2; i+=2) {
    display.drawCircle(display.width()/2, display.height()/2, i, SSD1306_WHITE);
    display.display();
    delay(1);
  }

  delay(2000);
}

void testfillcircle(void) {
  display.clearDisplay();

  for(int16_t i=max(display.width(),display.height())/2; i>0; i-=3) {
    // The INVERSE color is used so circles alternate white/black
    display.fillCircle(display.width() / 2, display.height() / 2, i, SSD1306_INVERSE);
    display.display(); // Update screen with each newly-drawn circle
    delay(1);
  }

  delay(2000);
}

void testdrawroundrect(void) {
  display.clearDisplay();

  for(int16_t i=0; i<display.height()/2-2; i+=2) {
    display.drawRoundRect(i, i, display.width()-2*i, display.height()-2*i,
      display.height()/4, SSD1306_WHITE);
    display.display();
    delay(1);
  }

  delay(2000);
}

void testfillroundrect(void) {
  display.clearDisplay();

  for(int16_t i=0; i<display.height()/2-2; i+=2) {
    // The INVERSE color is used so round-rects alternate white/black
    display.fillRoundRect(i, i, display.width()-2*i, display.height()-2*i,
      display.height()/4, SSD1306_INVERSE);
    display.display();
    delay(1);
  }

  delay(2000);
}

void testdrawtriangle(void) {
  display.clearDisplay();

  for(int16_t i=0; i<max(display.width(),display.height())/2; i+=5) {
    display.drawTriangle(
      display.width()/2  , display.height()/2-i,
      display.width()/2-i, display.height()/2+i,
      display.width()/2+i, display.height()/2+i, SSD1306_WHITE);
    display.display();
    delay(1);
  }

  delay(2000);
}

void testfilltriangle(void) {
  display.clearDisplay();

  for(int16_t i=max(display.width(),display.height())/2; i>0; i-=5) {
    // The INVERSE color is used so triangles alternate white/black
    display.fillTriangle(
      display.width()/2  , display.height()/2-i,
      display.width()/2-i, display.height()/2+i,
      display.width()/2+i, display.height()/2+i, SSD1306_INVERSE);
    display.display();
    delay(1);
  }

  delay(2000);
}

void testdrawchar(void) {
  display.clearDisplay();

  display.setTextSize(1);      // Normal 1:1 pixel scale
  display.setTextColor(SSD1306_WHITE); // Draw white text
  display.setCursor(0, 0);     // Start at top-left corner
  display.cp437(true);         // Use full 256 char 'Code Page 437' font

  // Not all the characters will fit on the display. This is normal.
  // Library will draw what it can and the rest will be clipped.
  for(int16_t i=0; i<256; i++) {
    if(i == '\n') display.write(' ');
    else          display.write(i);
  }

  display.display();
  delay(2000);
}

void testdrawstyles(void) {
  display.clearDisplay();

  display.setTextSize(1);             // Normal 1:1 pixel scale
  display.setTextColor(SSD1306_WHITE);        // Draw white text
  display.setCursor(0,0);             // Start at top-left corner
  display.println(F("Hello, world!"));

  display.setTextColor(SSD1306_BLACK, SSD1306_WHITE); // Draw 'inverse' text
  display.println(3.141592);

  display.setTextSize(2);             // Draw 2X-scale text
  display.setTextColor(SSD1306_WHITE);
  display.print(F("0x")); display.println(0xDEADBEEF, HEX);

  display.display();
  delay(2000);
}

void testscrolltext(void) {
  display.clearDisplay();

  display.setTextSize(2); // Draw 2X-scale text
  display.setTextColor(SSD1306_WHITE);
  display.setCursor(10, 0);
  display.println(F("scroll"));
  display.display();      // Show initial text
  delay(100);

  // Scroll in various directions, pausing in-between:
  display.startscrollright(0x00, 0x0F);
  delay(2000);
  display.stopscroll();
  delay(1000);
  display.startscrollleft(0x00, 0x0F);
  delay(2000);
  display.stopscroll();
  delay(1000);
  display.startscrolldiagright(0x00, 0x07);
  delay(2000);
  display.startscrolldiagleft(0x00, 0x07);
  delay(2000);
  display.stopscroll();
  delay(1000);
}

void testdrawbitmap(void) {
  display.clearDisplay();

  display.drawBitmap(
    (display.width()  - LOGO_WIDTH ) / 2,
    (display.height() - LOGO_HEIGHT) / 2,
    logo_bmp, LOGO_WIDTH, LOGO_HEIGHT, 1);
  display.display();
  delay(1000);
}

#define XPOS   0 // Indexes into the 'icons' array in function below
#define YPOS   1
#define DELTAY 2

void testanimate(const uint8_t *bitmap, uint8_t w, uint8_t h) {
  int8_t f, icons[NUMFLAKES][3];

  // Initialize 'snowflake' positions
  for(f=0; f< NUMFLAKES; f++) {
    icons[f][XPOS]   = random(1 - LOGO_WIDTH, display.width());
    icons[f][YPOS]   = -LOGO_HEIGHT;
    icons[f][DELTAY] = random(1, 6);
    Serial.print(F("x: "));
    Serial.print(icons[f][XPOS], DEC);
    Serial.print(F(" y: "));
    Serial.print(icons[f][YPOS], DEC);
    Serial.print(F(" dy: "));
    Serial.println(icons[f][DELTAY], DEC);
  }

  for(;;) { // Loop forever...
    display.clearDisplay(); // Clear the display buffer

    // Draw each snowflake:
    for(f=0; f< NUMFLAKES; f++) {
      display.drawBitmap(icons[f][XPOS], icons[f][YPOS], bitmap, w, h, SSD1306_WHITE);
    }

    display.display(); // Show the display buffer on the screen
    delay(200);        // Pause for 1/10 second

    // Then update coordinates of each flake...
    for(f=0; f< NUMFLAKES; f++) {
      icons[f][YPOS] += icons[f][DELTAY];
      // If snowflake is off the bottom of the screen...
      if (icons[f][YPOS] >= display.height()) {
        // Reinitialize to a random position, just off the top
        icons[f][XPOS]   = random(1 - LOGO_WIDTH, display.width());
        icons[f][YPOS]   = -LOGO_HEIGHT;
        icons[f][DELTAY] = random(1, 6);
      }
    }
  }
}

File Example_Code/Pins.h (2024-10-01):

#ifndef PINS_H
#define PINS_H

/////////////////PWM Bus (PCA9685)//////////////////

#define PB_SVO1        0
#define PB_SVO2        1
#define PB_SVO3        2
#define PB_SVO4        3
#define PB_SVO5        4
#define PB_CH5         5
#define PB_CH6         6
#define PB_CH7         7
#define PB_RED_L       8
#define PB_GREEN_L     9
#define PB_BLUE_L      10
#define PB_RED_R       11
#define PB_GREEN_R     12
#define PB_BLUE_R      13

/////////////Motor Driver (TB6612FNG)///////////////

#define PWMA1          21
#define PWMA2          33
#define PWMB1          34
#define PWMB2          35

////////////Shiftregister (74HC595PW)///////////////

#define SHCP           48
#define STCP           47
#define DS             42

//Shiftregister 1

#define SR_AIN1_1      0
#define SR_AIN2_1      1
#define SR_BIN1_1      2
#define SR_BIN2_1      3
#define SR_AIN1_2      4
#define SR_AIN2_2      5
#define SR_BIN1_2      6
#define SR_BIN2_2      7

//Shiftregister 2

#define SR_STBY1       8
#define SR_STBY2       9
#define SR_XSHT1       10
#define SR_XSHT2       11
#define SR_XSHT3       12
#define SR_XSHT4       13
#define SR_Q6          14
#define SR_Q7          15

/////////////////extern Buttons/////////////////////

#define T_E            16 //Button extern
#define T_M            41 //Button center
#define T_R            17 //Button right
#define T_L            18 //Button left

/////////////////////Inputs/////////////////////////

#define FLEX           14
#define VBAT           15

//RoboLight Front

#define PT_REF_L       1
#define PT_L_1         2
#define PT_L_0         4
#define PT_R_0         5
#define PT_R_1         6
#define PT_REF_R       7

//RoboLight Back

#define PT_L_3         10
#define PT_L_2         11
#define PT_R_2         12
#define PT_R_3         13

/////////////////////Outputs/////////////////////////

#define WHITE_L        36
#define WHITE_R        37
#define WHITE          38
#define RED            39
#define GREEN          40

///////////////////////I2C///////////////////////////

#define SDA            8
#define SCL            9
#define MPU6050_ADRESS 0x68
#define OLED_ADRESS    0x3C
#define TOF_ADRESS     0x29
#define PCA9685_ADRESS 0x40


#endif

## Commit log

2023-06-08 Big bug fix in the schematic
    Due to an input pullup resistor at pin 2 no program could be uploaded on the ESP32. Now the schematic was adapted and the resistor at pin 2 is omitted and replaced by an internal input pullup in the ESP32. This can be activated in the code.
    [Arche-RoboCore Komponenten.xlsx, Arche-RoboCore.brd, Arche-RoboCore.sch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]
2023-06-17 adding light sensors in hardware/hardware
2023-06-22 Seperated all files. Added calibration and a basic line following program.
2023-09-17 Fixes
    -Change the position of the inner photo transistors und RGB leds
    [RoboCore Light sensor bar v1.f3d, RoboCore Light sensor bar.brd, RoboCore Light sensor bar.sch]
2023-11-27 Raus mit die gestohlen

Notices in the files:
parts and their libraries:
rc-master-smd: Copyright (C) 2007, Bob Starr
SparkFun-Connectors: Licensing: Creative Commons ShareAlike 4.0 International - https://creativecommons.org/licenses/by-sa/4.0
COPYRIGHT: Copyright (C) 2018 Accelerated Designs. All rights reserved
